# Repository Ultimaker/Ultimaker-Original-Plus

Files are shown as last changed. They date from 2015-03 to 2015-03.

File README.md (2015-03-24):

# Ultimaker-Original-Plus
Bill of Materials and parts for UM-original +

In this repository you will find the documentation and source files for all parts in the Ultimaker-Original+ 3D printer. In the Bill Of Materials (BOM) repository all the parts are numbered and named with the correct amounts. The parts can be found in all the separate directories. 

A lot of parts are lasercut. In the BOM these are marked by the blue colour. The lasercut files can be found separately in the laser file directory. The electronic files can be found in the directory 1091 main board V2.1.1; 1146 ultipanel rev 1.1 and 1155 Print Table Heated Bed.

The manual will explain how to put all files together. 

If you are missing a part or information feel free to file an issue on github.

Harma Woldhuis 
Ultimaker Research and Development

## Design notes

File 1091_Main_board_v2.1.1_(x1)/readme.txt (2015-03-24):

The UltiMainboard 2.x.x electronics are released under GPLv2 license.
And are based on the origonal Ultimaker electronics design by Jan-Jaap Schuurman, Siert Wijnia and ErikDeBruijn at http://reprap.org/wiki/Ultimaker's_v1.5.7_PCB
As well as the ArduinoMega2560 by Arduino: http://arduino.cc/en/Main/arduinoBoardMega2560

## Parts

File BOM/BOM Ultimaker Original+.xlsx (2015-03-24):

 | Ultimaker Original+ |  |  | lasercut parts
 |  |  |  | injection moulded parts
Total quantity parts | 662
Partnummer |  | Naam | Quantity
1002 | A | Front Panel | 1
1003 | A | Back Panel | 1
1004 | A | Left Panel | 1
1005 | A | Right Panel | 1
1006 | A | Top Panel | 1
1007 | A | Bottom Panel | 1
1008 | A | Reel Holder Part A | 1
1009 | A | Reel Holder Mounting Plate | 1
1010 | A | Velcro parts | 4
1011 | A | Y-linear shaft | 2
1012 | A | X-linear shaft | 2
1016 | A | Feeder Quick Fit Coupling | 1
1017 | A | Feeder Motor | 1
1018 | A | Feeder Base Plate Motor Side | 1
1021 | A | Ball Bearing 688-2RS | 10
1023 | A | Limit Switch, Black Long Wire | 1
1025 | A | Limit Switch, Blue Wire | 1
1026 | A | Limit Switch, Red Wire | 1
1028 | A | Z-linear Shaft | 2
1029 | A | Bearing Cap Outside | 8
1031 | A | Feeder Bolt Clip | 1
1032 | A | Feeder Clamp A | 1
1033 | A | Feeder Clamp C | 1
1034 | A | Feeder Clamp B | 1
1035 | A | Feeder Lever | 1
1036 | A | Feeder Wheel | 1
1037 | A | Print Head Coupling Plate | 1
1039 | A | Feeder U bar | 1
1041 | A | Feeder Small Gear | 1
1044 | A | Z-shaft Cap Top | 2
1045 | A | Bearing Cap Inside | 6
1046 | A | Print Head Shaft X,Y | 2
1048 | A | Print Head Hot End Holder | 1
1049 | A | Aluminum Heater Block | 1
1053 | A | Hot End Isolator Tube | 1
1054 | A | Nozzle 0.4mm | 1
1055 | B | Hot End Isolator Coupler | 1
1056 | B | Sintered Bushing | 4
1057 | B | Z-shaft Cap Bottom | 2
1058 | B | Print Head Back | 1
1059 | B | Print Head Top Cap | 1
1061 | B | Print Head Bottom Cap | 1
1062 | B | Print Head Left | 1
1063 | B | Print Head Front | 1
1064 | B | Print Head Right | 1
1065 | A | Linear Bearing LM6LUU | 2
1067 | A | PEEK Isolator | 1
1069 | A | Tube Coupling Collet | 1
1071 | A | Clamp Clip | 2
1082 | A | X,Y-Motor | 2
1084 | A | Timing Pulley 5mm Shaft | 2
1085 | A | Timing Belt B100 MXL | 2
1086 | A | Timing Belt B300 MXL | 4
1088 | A | Timing Pulley 8mm Shaft | 10
1089 | A | Right Side Controller | 1
1091 | B | Main Board V2.1.1 | 1
1092 | A | Left Side Controller | 1
1093 | A | Bottom Cover Controller | 1
1095 | A | Top Cover Controller | 1
1097 | A | Spiral Sleeve | 1
1116 | A | Reel Holder Part B | 4
1117 | A | Sliding Block Part A | 8
1118 | A | Sliding Block Part B | 1
1119 | A | Sliding Block Part C | 2
1121 | A | Sliding Block Part D | 4
1122 | A | Sliding Block Part E | 1
1126 | A | Feeder Middle Plate | 1
1128 | A | Feeder Big Gear | 1
1129 | A | Knob | 1
1131 | A | Cable Duct Front | 2
1132 | A | Cable Duct Back | 2
1133 | A | Feeder Knurled Bolt | 1
1134 | A | Capnut M8 | 1
1136 | A | Washer M8 | 2
1137 | A | Nut M8 | 1
1139 | A | Spacer, White, 3.2x5x16 | 4
1142 | A | Ball Bearing 693ZZ | 1
1143 | A | Feeder Spring D2110 | 1
1144 | A | USB Cable | 1
1146 | A | Ultipanel Rev 1.1 | 1
1152 | A | Table Spring D2150 | 3
1154 | A | Print Table Glass | 1
1155 | A | Print Table Heated Bed | 1
1159 | A | Z-Motor with Trapezoidal Lead Screw | 1
1170 | A | Square Flanged Linear Bearing LMK12LUU | 2
1171 | A | Double flat Cable 10 Wire | 1
1183 | B | Heated Bed Cable | 1
1185 | A | PT100 B sensor | 1
1187 | A | Trapezoidal Lead Nut | 1
1201 | B | Washer Large M3 | 14
1202 | B | ISO 7380 M3x10 | 23
1203 | B | ISO 7380 M3x12 | 11
1204 | B | ISO 7380 M3x16 | 75
1205 | B | ISO 7380 M3x14 | 7
1206 | B | ISO 7380 M3x20 | 12
1207 | B | ISO 7380 M3x25 | 12
1208 | B | ISO 7380 M3x30 | 16
1209 | B | Nut M3 | 110
1211 | A | Set Screw M4x4 | 12
1214 | A | ISO 7040 Nut M3 Prev. torque A2 | 25
1217 | A | ISO 7380 M4x10 A2 | 8
1225 | A | tape | 1
1226 | A | grease | 1
1227 | A | Hex Key Screwdriver 2 | 1
1228 | A | pritt | 1
1238 | A | Power Adapter 24v-220W | 1
1241 | A | Motor Spacer | 2
1243 | A | Heated Bed Cable Clip | 1
1250 | A | SD card 4G | 1
1256 | A | Build Platform Glass Retainer Back | 4
1257 | A | Knurled Nut Platform | 3
1266 | C | Bowden tube | 1
1288 | A | Washer M6 | 3
1315 | A | Jumper | 2
1326 | A | Warning sticker | 1
1348 | A | Bolt M3x4 | 2
1362 | A | Tap Fix 2.5x14 mm staal verzinkt bolkop porzidrive | 2
1355 | B | Heated Bed Bolt 8 mm
1356 | B | Heated Bed Bolt 20 mm
1402 | A | Hex Key Wrench 2.5 | 1
1501 | D | Print Head Fancap Metal | 1
1502 | A | Spacer 3.2x6x8 | 8
1503 | A | Sliding Block Part F | 8
1504 | A | Sliding Block Part G | 4
1505 | A | print table cap | 1
1506 | A | print table cap side A | 1
1507 | A | print table cap side B | 1
1508 | A | print table cap middle | 2
1509 | A | Feeder cap | 1
1510 | A | Feeder wheelcap | 1
1511 | A | Short reel holder part A | 2
1512 | A | Print Head Fan 24VDC | 1
1513 | A | Heater Cartridge 24V 40W | 1
1514 | A | Metal Cable Clamp | 1
1522 | A | ulticontroller window | 1
1524 | B | copper grease | 1
1528 | A | Feeder Plate Non Motor Side | 1
1529 | A | Electronics Cover Plate | 1
1530 | A | X-Y calibration sticks | 2
1540 | A | Nylon M3 nut | 10
1541 | A | Nylon M3x 12 Panhead | 6
1542 | A | Nylon M3x 25 Panhead | 4
1545 | A | Spacer 3.2x6x3 | 2
1680 | A | Print Head Thumb screw 62mm | 4
1681 | A | Timingbelt spring | 4
1805 | 01 | Power Cable EU Type C13 CE
1806 | 01 | Power Cable UK Type C13 CE
1807 | 01 | Power Cable AU Type C13 CE
1808 | 01 | Power Cable US Type C13 CE
1818 | B | Print Table Base Plate | 1
Reserve onderdelen
1201 | B | Washer Large M3 | 5
1202 | B | ISO 7380 M3x10 | 5
1203 | B | ISO 7380 M3x12 | 5
1204 | B | ISO 7380 M3x16 | 5
1205 | B | ISO 7380 M3x14 | 5
1206 | B | ISO 7380 M3x20 | 5
1207 | B | ISO 7380 M3x25 | 5
1208 | B | ISO 7380 M3x30 | 5
1209 | B | Nut M3 | 10
1211 | A | Set Screw M4x4 | 5
1214 | A | ISO 7040 Nut M3 Prev. torque A2 | 10
1215 | A | ISO 10642 M3x8 A2 | 2
1216 | A | ISO 10642 M3x20 A2 | 2
1217 | A | ISO 7380 M4x10 A2 | 2
1540 | A | Nylon M3 nut | 2
1541 | A | Nylon M3x 12 Panhead | 2
1542 | A | Nylon M3x 25 Panhead | 2

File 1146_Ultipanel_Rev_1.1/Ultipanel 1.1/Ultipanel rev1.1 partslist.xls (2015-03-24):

Part | RS partno | Manufacturer partno | Value | Device | Package | Remarks
724-3175 | 724-3175 | RS 724-3175 |  |  |  | buzzer
DS1 | 532-6818 | Displaytech 204A-CC-BC-3LP |  |  |  | lcd screen Blue/White, soldered with header 2.54 mm
EC11E15244B2 | 729-5609 | ALPS EC11E15244B2 |  |  |  | 20mm Vertical encoder 15 Pulses 30 DET
EXP1 | 473-8349 | TE connectivity 1-1634689-0 |  |  |  | right angle!
EXP2 | 473-8349 | TE connectivity 1-1634689-0 |  |  |  | right angle!
HRS163_REVERSE | 685-0788 | Hirose DM1B-DSF-PEJ(82)
R3 | 731-2883 | Panasonic EVM3YSX50B14 | 10K
RBEEP | 708-6014 |  | 440R |  | 0805
RLED | 721-9725 |  | 68R |  | 1206
SHIFT | 483-6544P | NXP 74HC4050D | 4050D |  |  | levelshifter
T4 | 294-312 | Magnatec 2N3904 | 2N3904
JP1 | not used

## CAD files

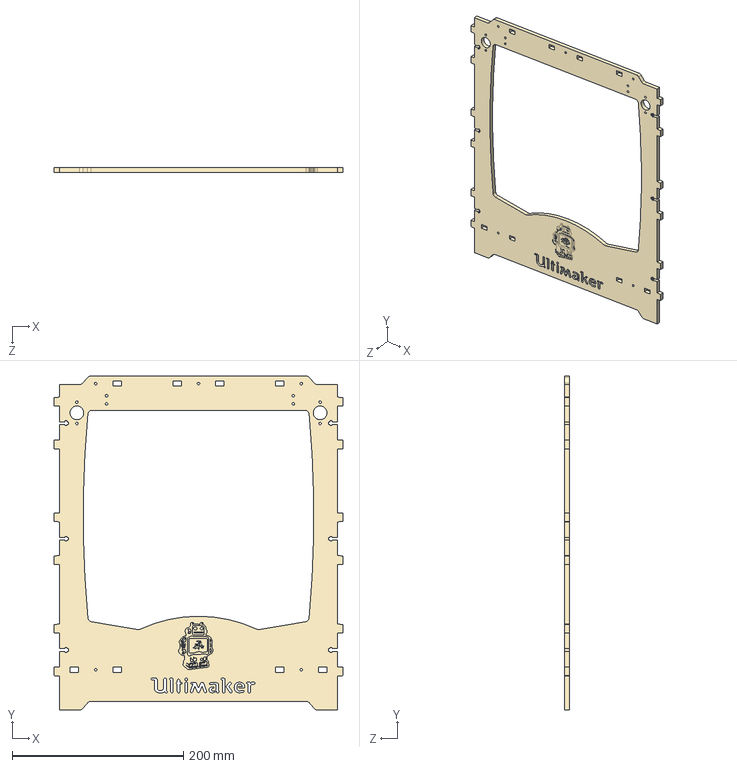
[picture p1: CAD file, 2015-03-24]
1002_Front_Panel/1002-A2P-A.STEP
337.2 x 390.0 x 6.00 mm

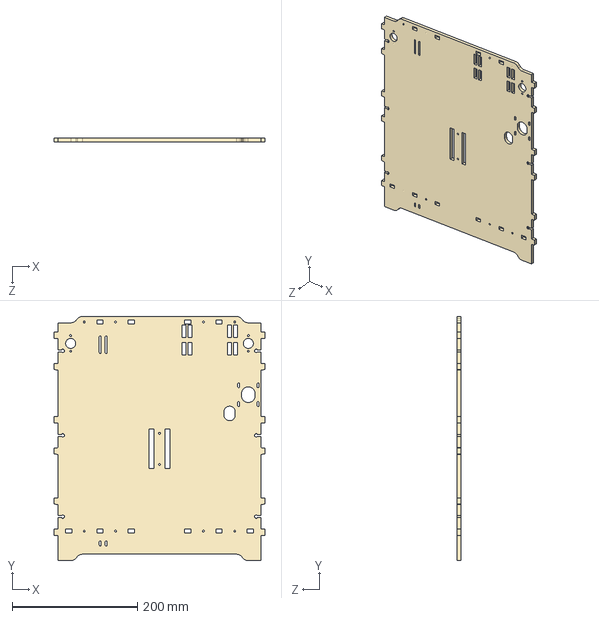
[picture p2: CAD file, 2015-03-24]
1003_Back_Panel/1003-A2P-A.STEP
337.2 x 390.0 x 6.00 mm

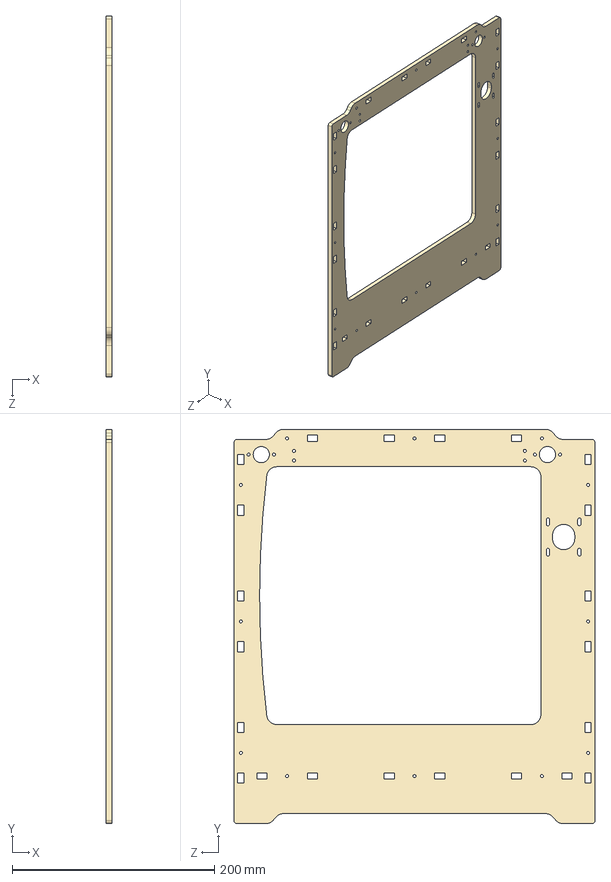
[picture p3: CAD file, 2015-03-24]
1004_Left_Panel/1004-A2P-A.STEP
6.00 x 390.0 x 357.0 mm

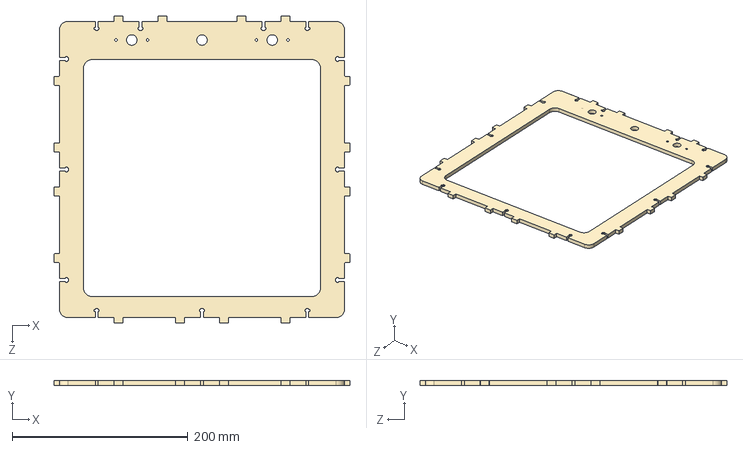
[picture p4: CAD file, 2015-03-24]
1006_Top_Panel/1006-A2P-A.STEP
337.2 x 6.00 x 349.7 mm

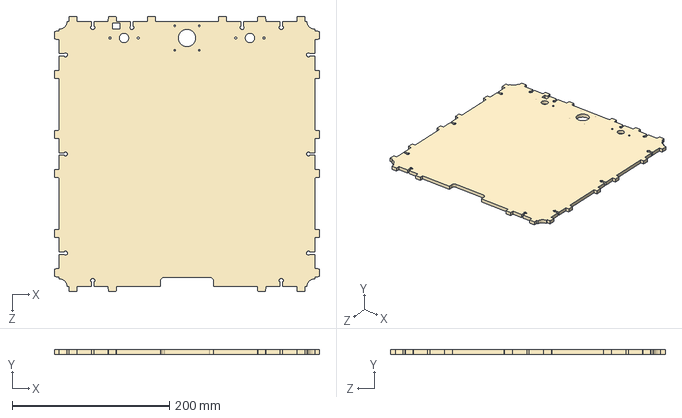
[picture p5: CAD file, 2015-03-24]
1007_Bottom_Panel/1007-A2P-A.STEP
337.2 x 6.00 x 349.7 mm

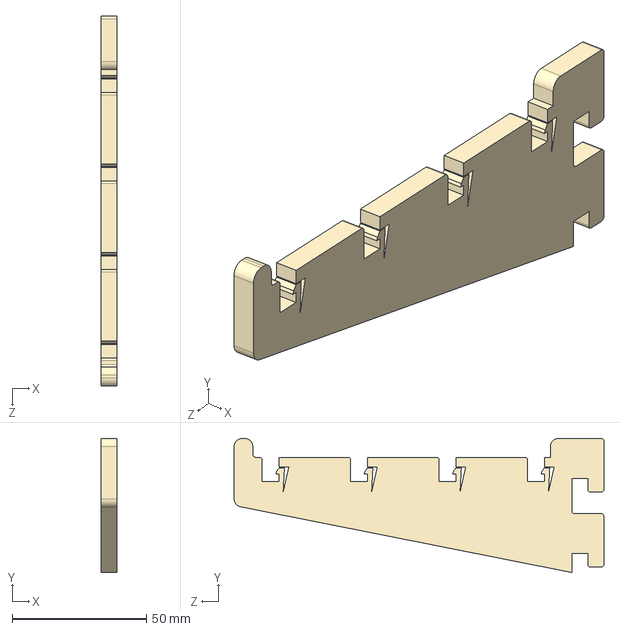
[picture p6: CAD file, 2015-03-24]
1008_Reel_Holder_Part_A/1008-A2P-A.STEP
6.00 x 50.0 x 138.0 mm

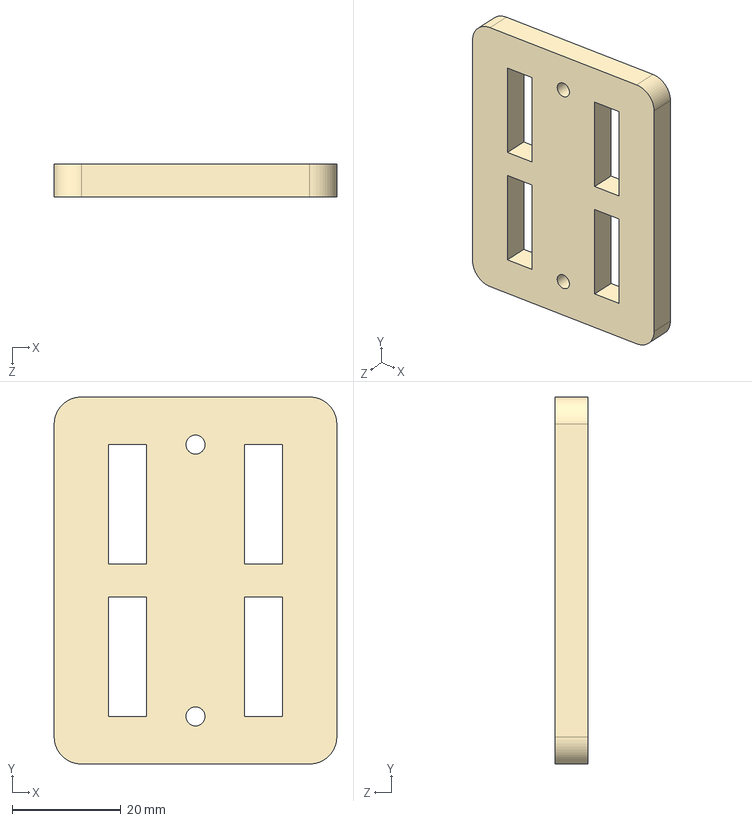
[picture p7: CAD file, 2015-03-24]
1009_Reel_Holder_Mounting_Plate/1009-A2P-A.STEP
52.0 x 67.5 x 6.00 mm

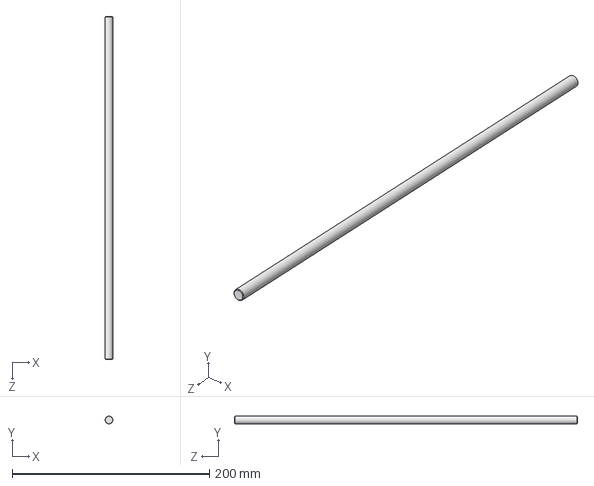
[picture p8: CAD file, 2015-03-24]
1011_Y-linear_shaft/1011-A2P-A.STEP
7.99 x 8.00 x 348.0 mm

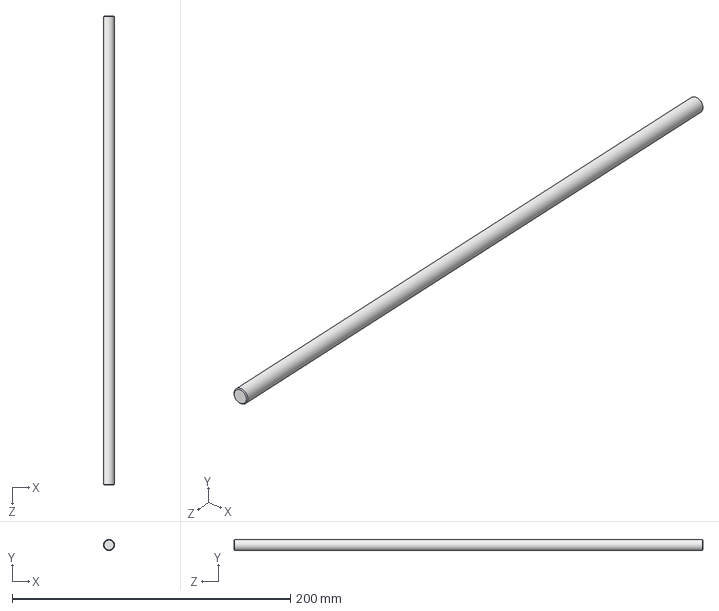
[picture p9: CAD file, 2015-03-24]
1012_X-linear_shaft/1012-A2P-A.STEP
7.99 x 8.00 x 337.0 mm

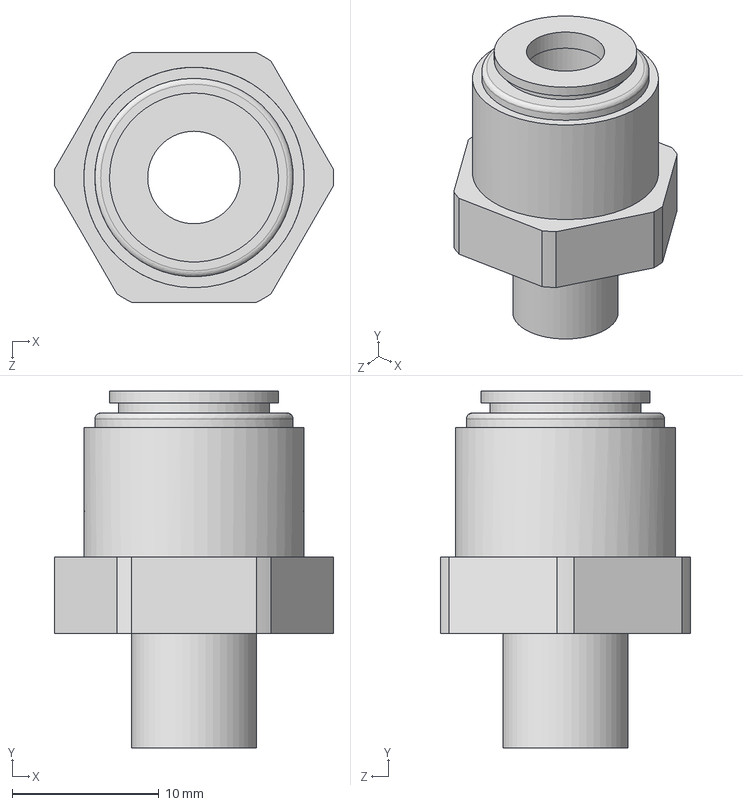
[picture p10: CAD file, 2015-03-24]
1016_Feeder_Quick_Fit_Coupling/1016-Z1P-A.STEP
19.0 x 24.3 x 17.0 mm

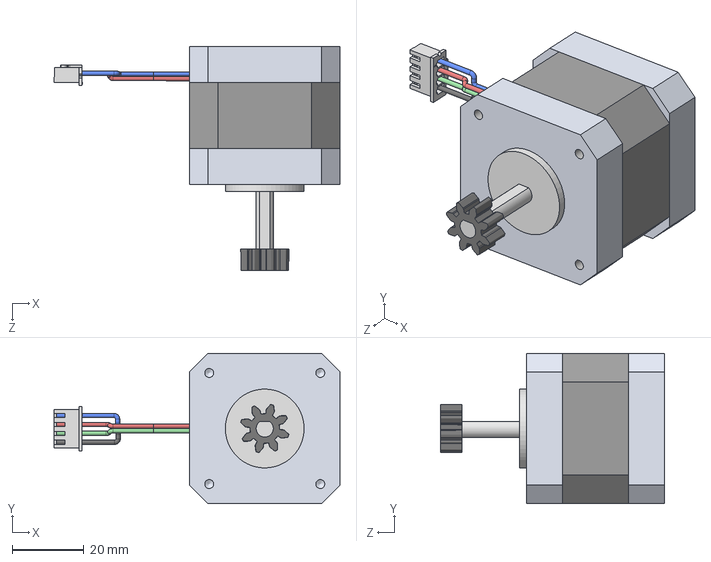
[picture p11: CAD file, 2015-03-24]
1017_Feeder_Motor/1017-Z1P-A.STEP
79.8 x 42.0 x 62.5 mm

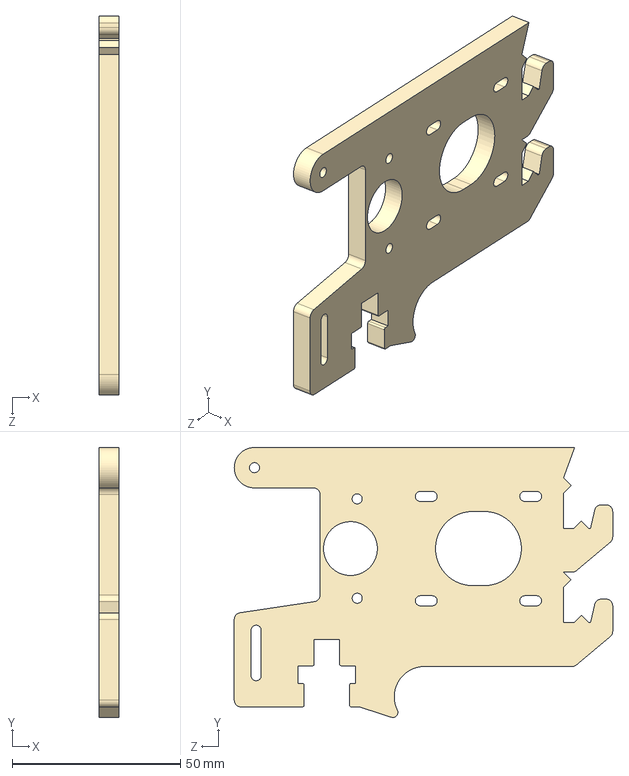
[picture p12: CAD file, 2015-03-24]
1018_Feeder_Base_Plate_Motor_Side/1018-A2P-A.STEP
6.00 x 80.1 x 112.4 mm

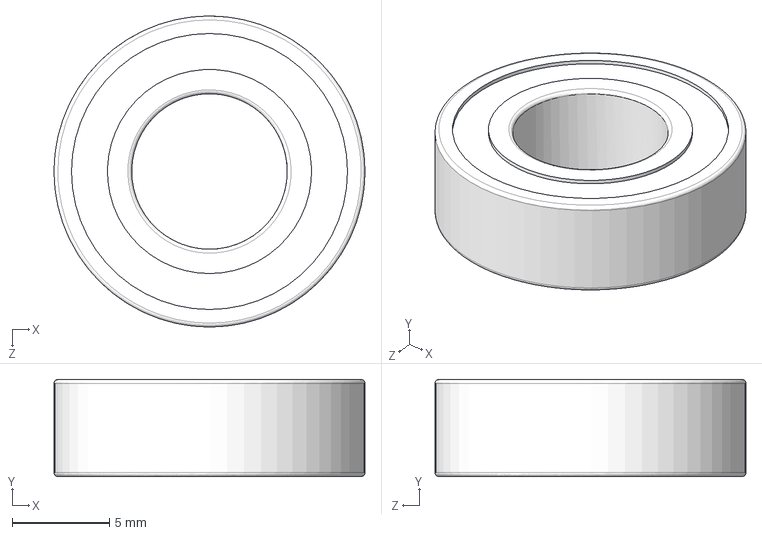
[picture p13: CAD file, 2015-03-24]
1021_Ball_Bearing_688-2RS/1021-Z1P-A.STEP
16.0 x 5.00 x 16.0 mm

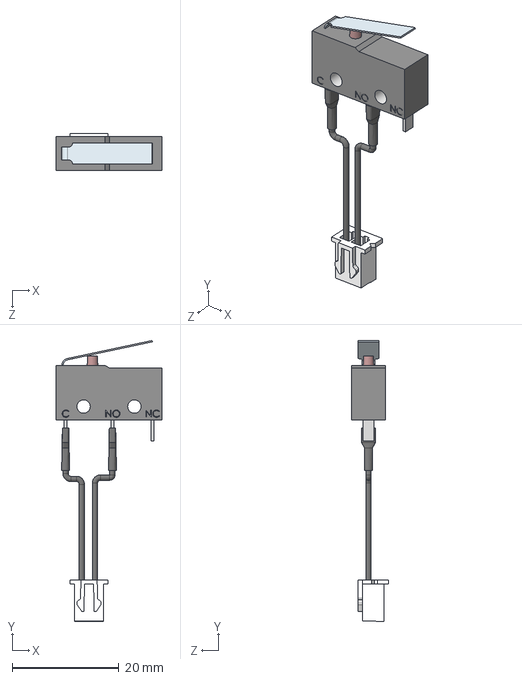
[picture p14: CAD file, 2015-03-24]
1023_Limit_Switch,_Black_Long_Wire/1023-Z1P-A.STEP
19.8 x 52.7 x 6.90 mm

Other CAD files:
1005_Right_Panel/1005-A2P-A.STEP
1025_Limit_Switch,_Blue_Wire/1025-Z1P-A.STEP
1026_Limit_Switch,_Red_Wire/1026-Z1P-A.STEP
1028_Z-linear_Shaft/1028-A2P-A.STEP
1029_Bearing_Cap_Outside/1029-A2P-A.STEP
1031_Feeder_Bolt_Clip/1031-A2P-A.STEP
1032_Feeder_Clamp_A/1032-A2P-A.STEP
1033_Feeder_Clamp_C/1033-A2P-A.STEP
1034_Feeder_Clamp_B/1034-A2P-A.STEP
1035_Feeder_Lever/1035-A2P-A.STEP
1036_Feeder_Wheel/1036-A2P-A.STEP
1037_Print_Head_Coupling_Plate/1037-A2P-A.STEP
1039_Feeder_U_bar/1039-A2P-A.STEP
1041_Feeder_Small_Gear/1041-A2P-A.STEP
1044_Z-shaft_Cap_Top/1044-A2P-A.STEP
1045_Bearing_Cap_Inside/1045-A2P-A.STEP
1046_Print_Head_Shaft_X,Y/1046-A2P-A.STEP
1048_Print_Head_Hot_End_Holder/1048-A2P-A.STEP
1049_Aluminum_Heater_Block/1049-A2P-A.STEP
1053_Hot_End_Isolator_Tube/1053-A2P-A.STEP
1054_Nozzle_0.4mm/1054-A2P-A.STEP
1055_Hot_End_Isolator_Coupler/1055-A2P-B.STEP
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

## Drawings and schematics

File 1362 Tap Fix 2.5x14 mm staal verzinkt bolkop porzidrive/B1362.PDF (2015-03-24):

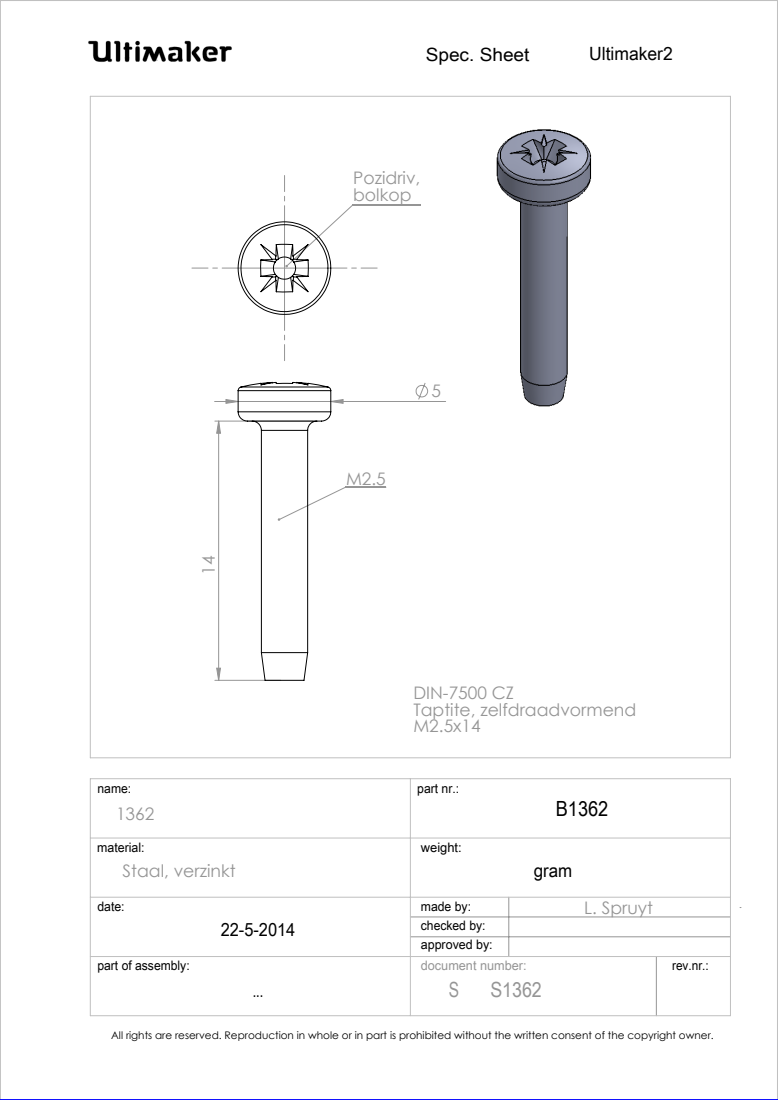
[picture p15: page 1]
part of assembly:; rev.nr.:; part nr.:; made by:; Spec. Sheet; approved by:; checked by:; L. Spruyt; document number: S S1362; Staal, verzinkt; DIN-7500 CZ Taptite, zelfdraadvormend

All rights are reserved. Reproduction in whole or in part is prohibited without the written consent of the copyright owner.

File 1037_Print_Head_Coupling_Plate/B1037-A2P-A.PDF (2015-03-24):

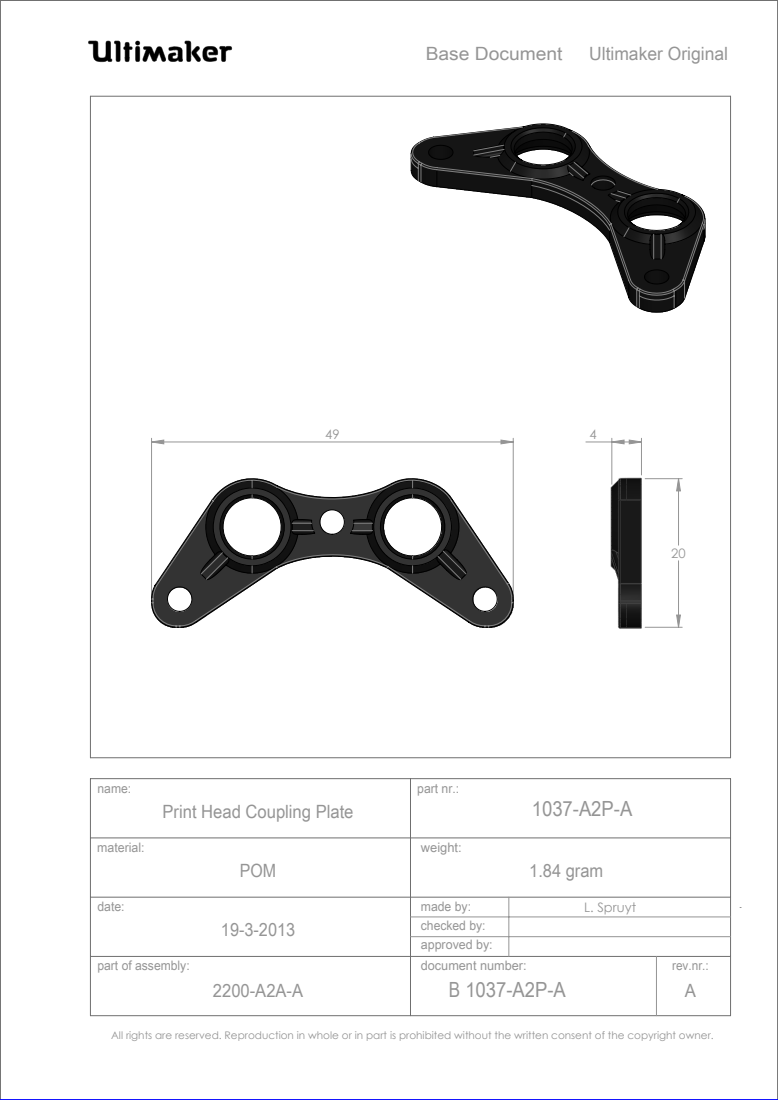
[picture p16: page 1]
POM; 1.84 gram; Ultimaker Original; part of assembly:; rev.nr.:; part nr.:; made by:; Base Document; approved by:; checked by:; L. Spruyt; document number: B 1037-A2P-A

name:
Print Head Coupling Plate

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

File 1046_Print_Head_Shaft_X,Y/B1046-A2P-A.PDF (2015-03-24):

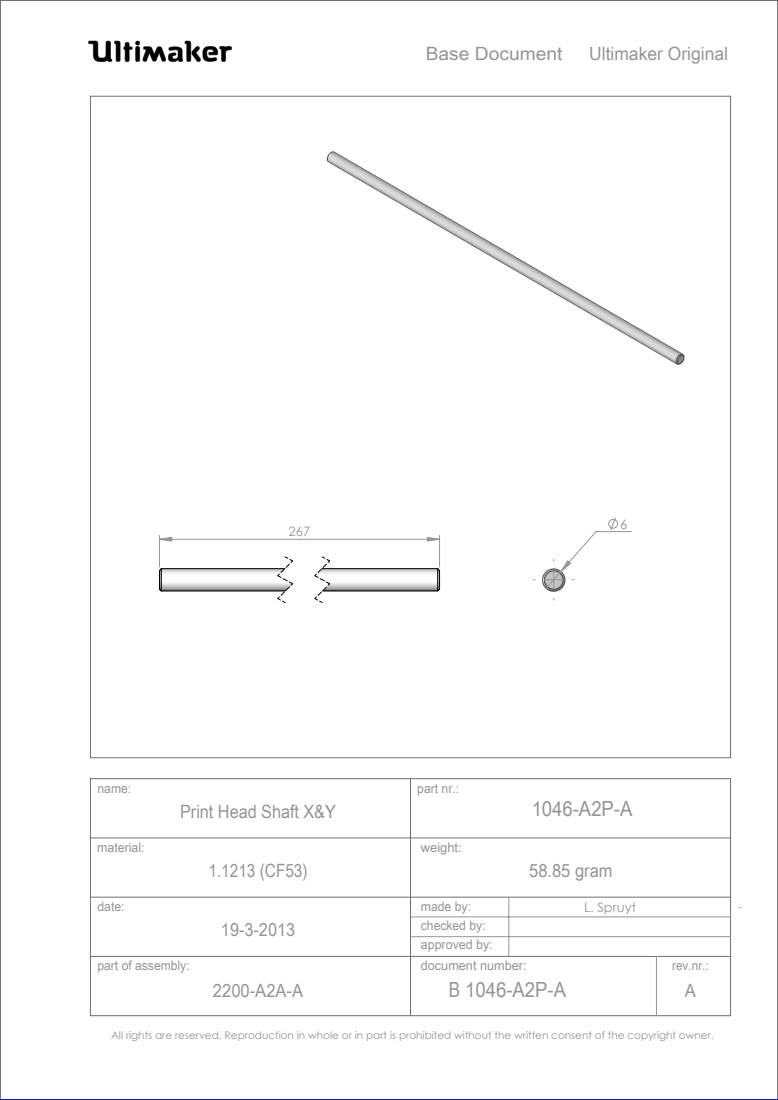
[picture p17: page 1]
58.85 gram; Ultimaker Original; part of assembly:; rev.nr.:; part nr.:; made by:; Base Document; approved by:; checked by:; L. Spruyt; document number: B 1046-A2P-A

Print Head Shaft X&Y

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

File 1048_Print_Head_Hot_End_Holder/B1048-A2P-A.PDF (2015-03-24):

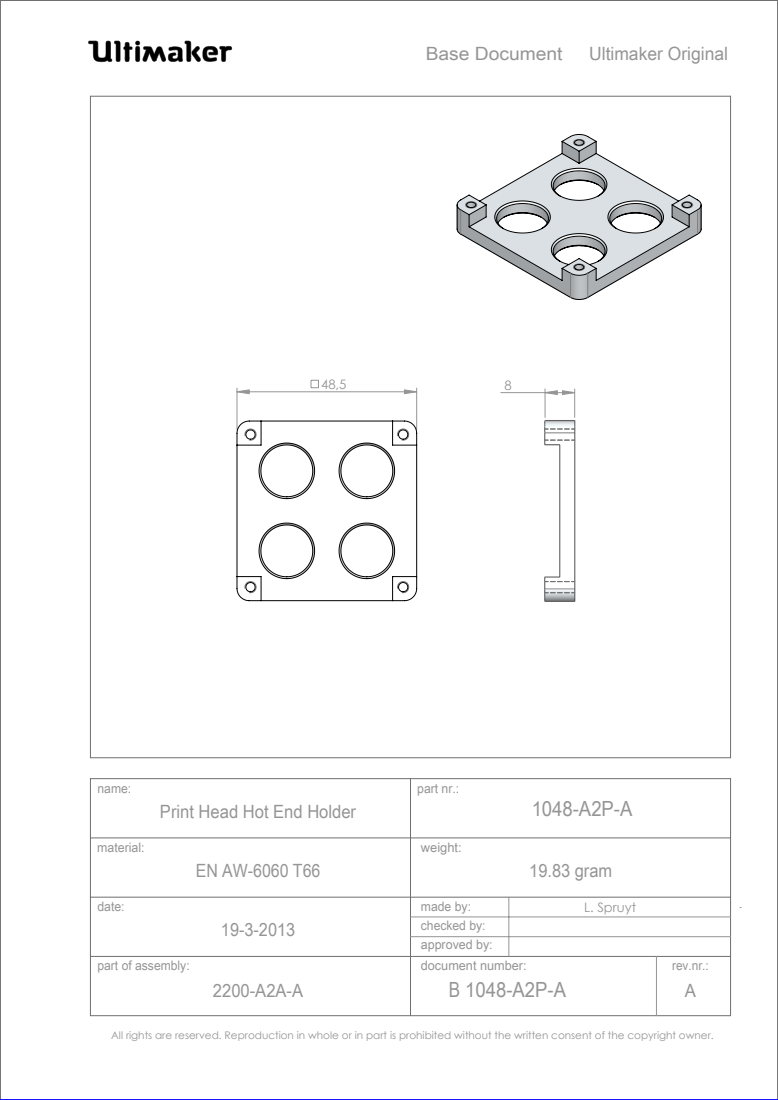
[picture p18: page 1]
19.83 gram; Ultimaker Original; part of assembly:; rev.nr.:; part nr.:; made by:; Base Document; approved by:; checked by:; L. Spruyt; document number: B 1048-A2P-A

name:
Print Head Hot End Holder

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

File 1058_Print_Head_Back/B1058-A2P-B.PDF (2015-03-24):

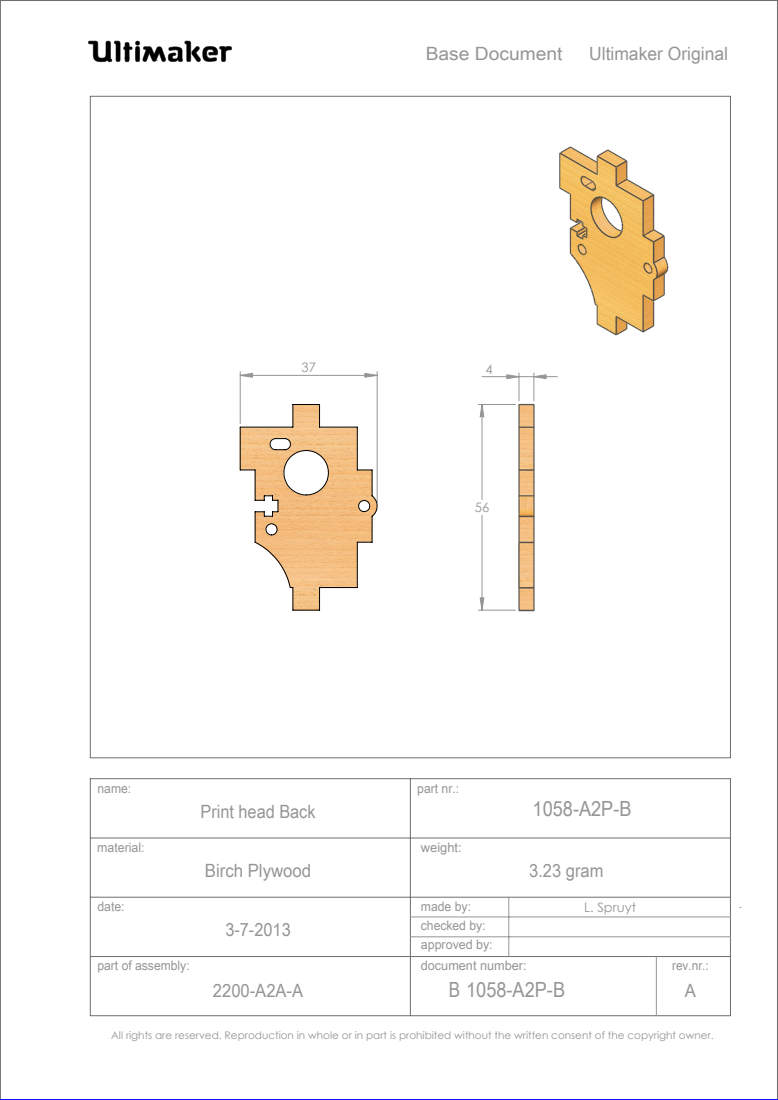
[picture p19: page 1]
Birch Plywood; 3.23 gram; Ultimaker Original; part of assembly:; rev.nr.:; part nr.:; made by:; Base Document; approved by:; checked by:; L. Spruyt; document number: B 1058-A2P-B

Print head Back

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

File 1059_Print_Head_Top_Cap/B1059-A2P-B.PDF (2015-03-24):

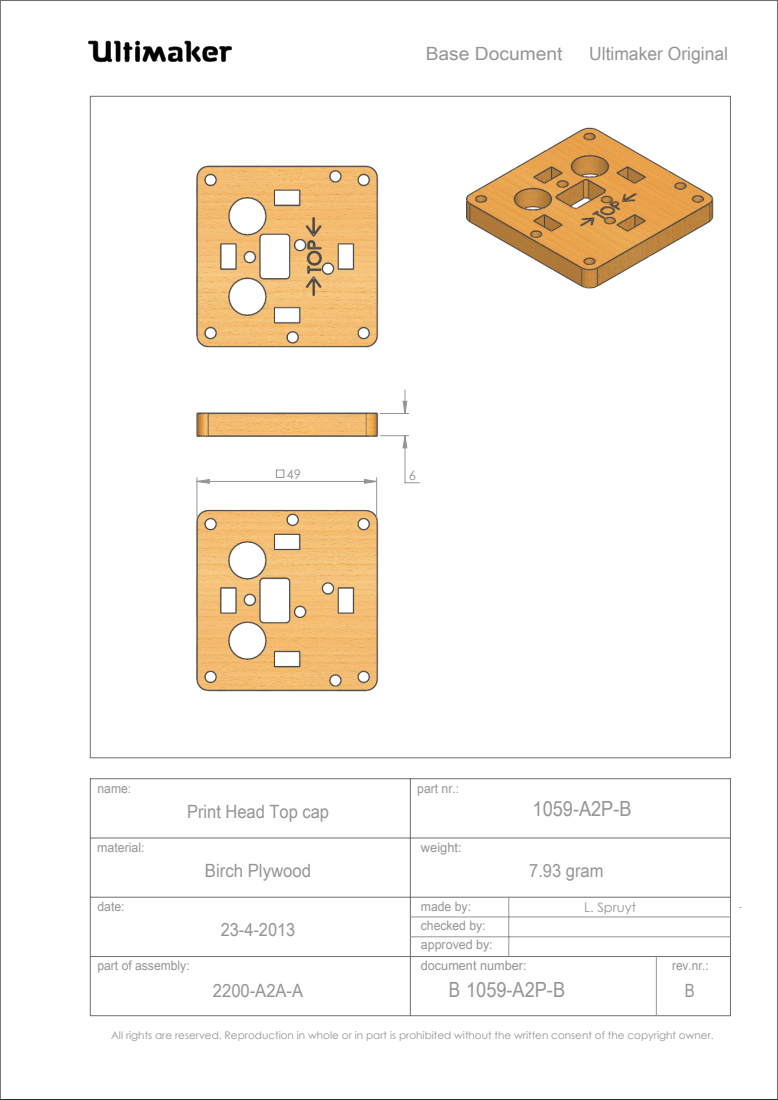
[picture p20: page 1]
Birch Plywood; 7.93 gram; Ultimaker Original; part of assembly:; rev.nr.:; part nr.:; made by:; Base Document; approved by:; checked by:; L. Spruyt; document number: B 1059-A2P-B

Print Head Top cap

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

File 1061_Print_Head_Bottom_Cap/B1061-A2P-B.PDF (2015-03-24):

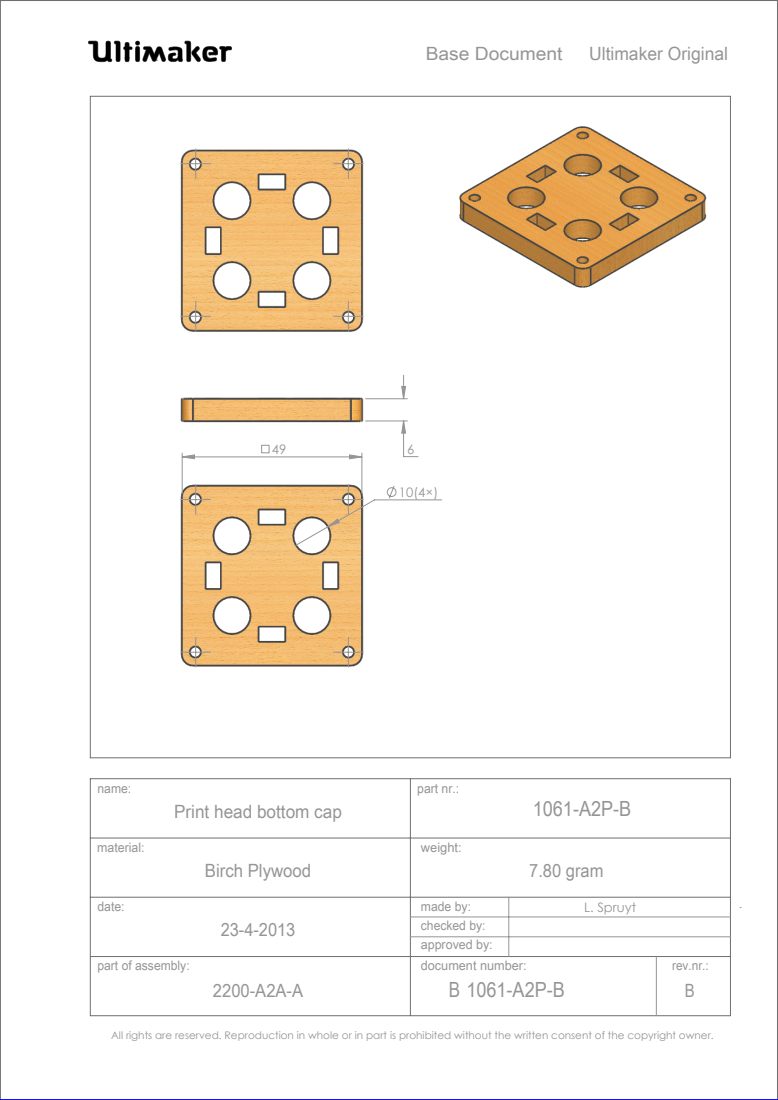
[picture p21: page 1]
Birch Plywood; 7.80 gram; Ultimaker Original; part of assembly:; rev.nr.:; part nr.:; made by:; Base Document; approved by:; checked by:; L. Spruyt; document number: B 1061-A2P-B

Print head bottom cap

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

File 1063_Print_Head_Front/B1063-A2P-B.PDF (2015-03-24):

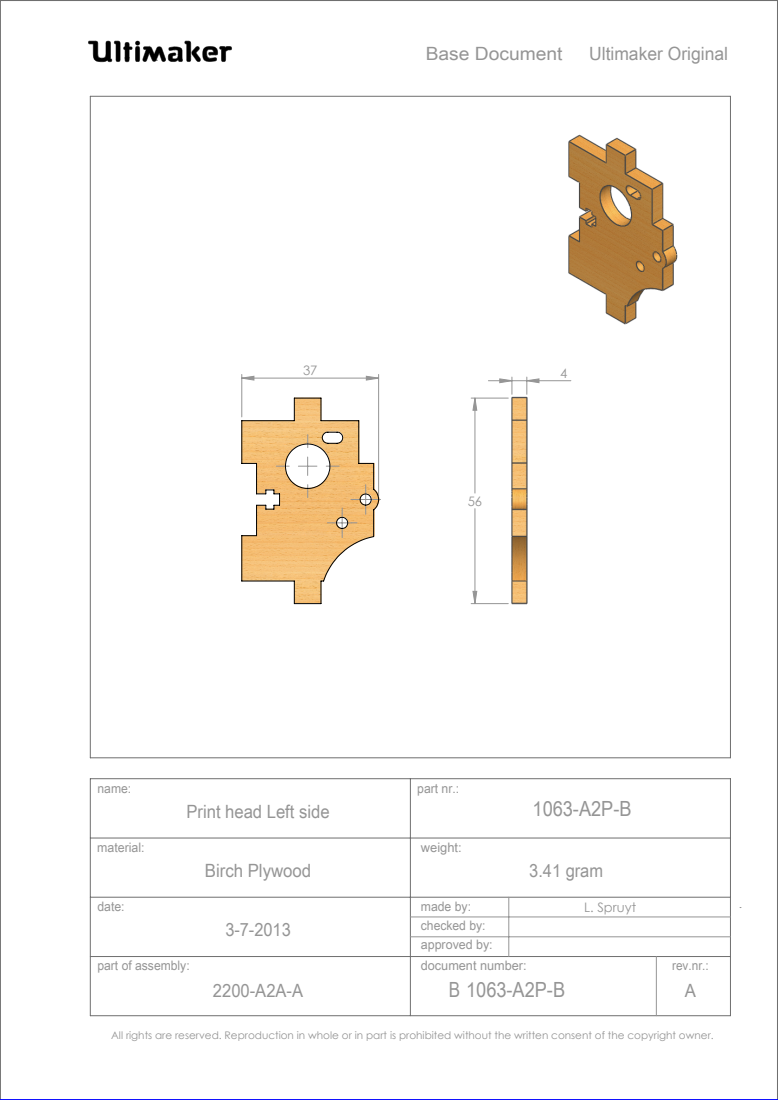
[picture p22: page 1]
Birch Plywood; 3.41 gram; Ultimaker Original; part of assembly:; rev.nr.:; part nr.:; made by:; Base Document; approved by:; checked by:; L. Spruyt; document number: B 1063-A2P-B

Print head Left side

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

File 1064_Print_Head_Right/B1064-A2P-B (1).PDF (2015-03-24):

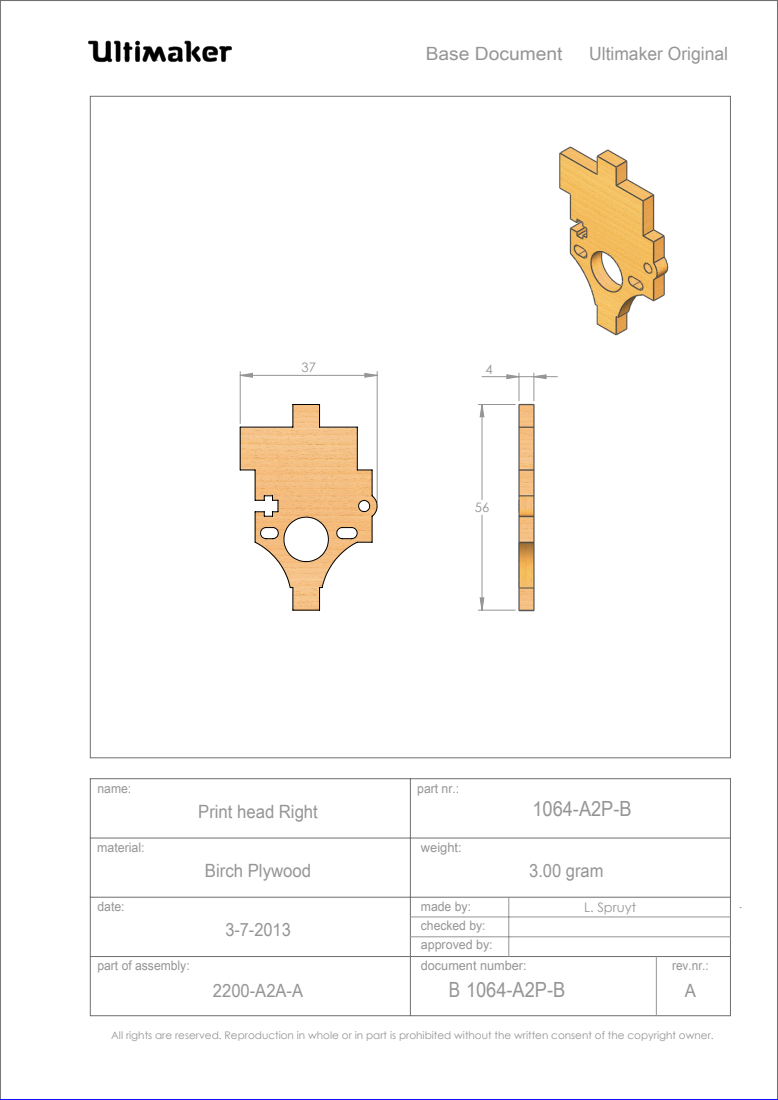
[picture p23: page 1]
Birch Plywood; 3.00 gram; Ultimaker Original; part of assembly:; rev.nr.:; part nr.:; made by:; Base Document; approved by:; checked by:; L. Spruyt; document number: B 1064-A2P-B

Print head Right

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

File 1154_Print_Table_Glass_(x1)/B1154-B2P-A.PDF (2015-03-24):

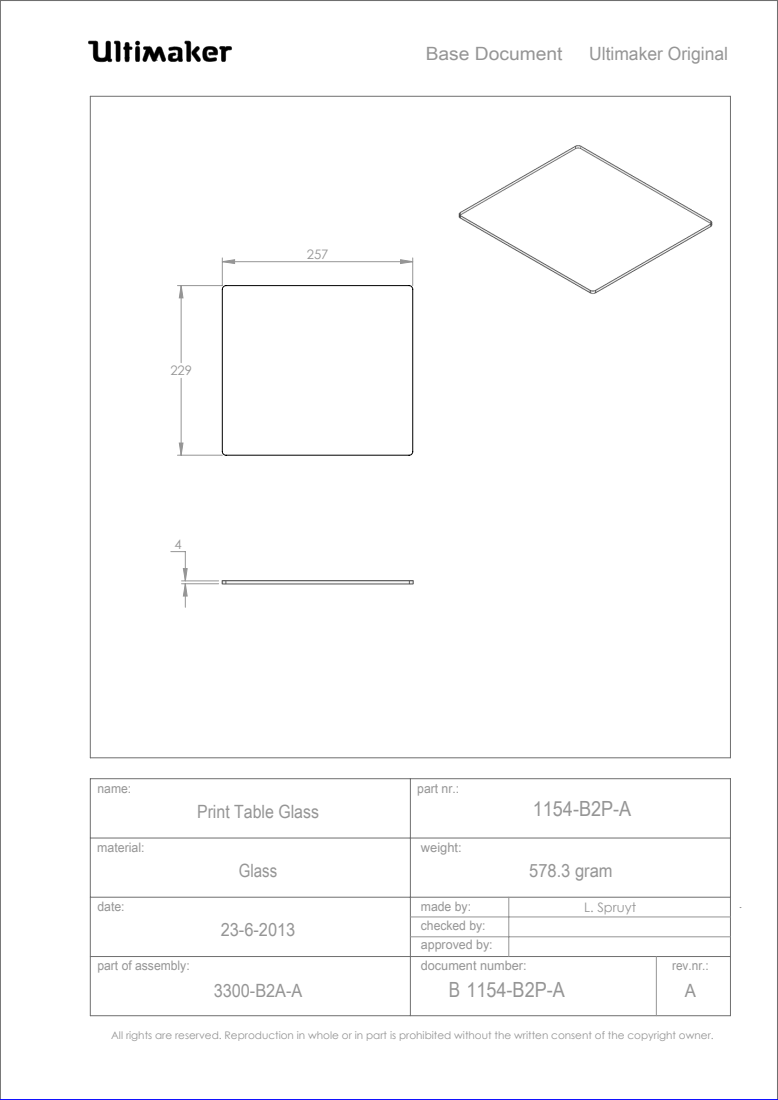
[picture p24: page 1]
Glass; 578.3 gram; Ultimaker Original; part of assembly:; rev.nr.:; part nr.:; made by:; Base Document; approved by:; checked by:; L. Spruyt; document number: B 1154-B2P-A

Print Table Glass

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

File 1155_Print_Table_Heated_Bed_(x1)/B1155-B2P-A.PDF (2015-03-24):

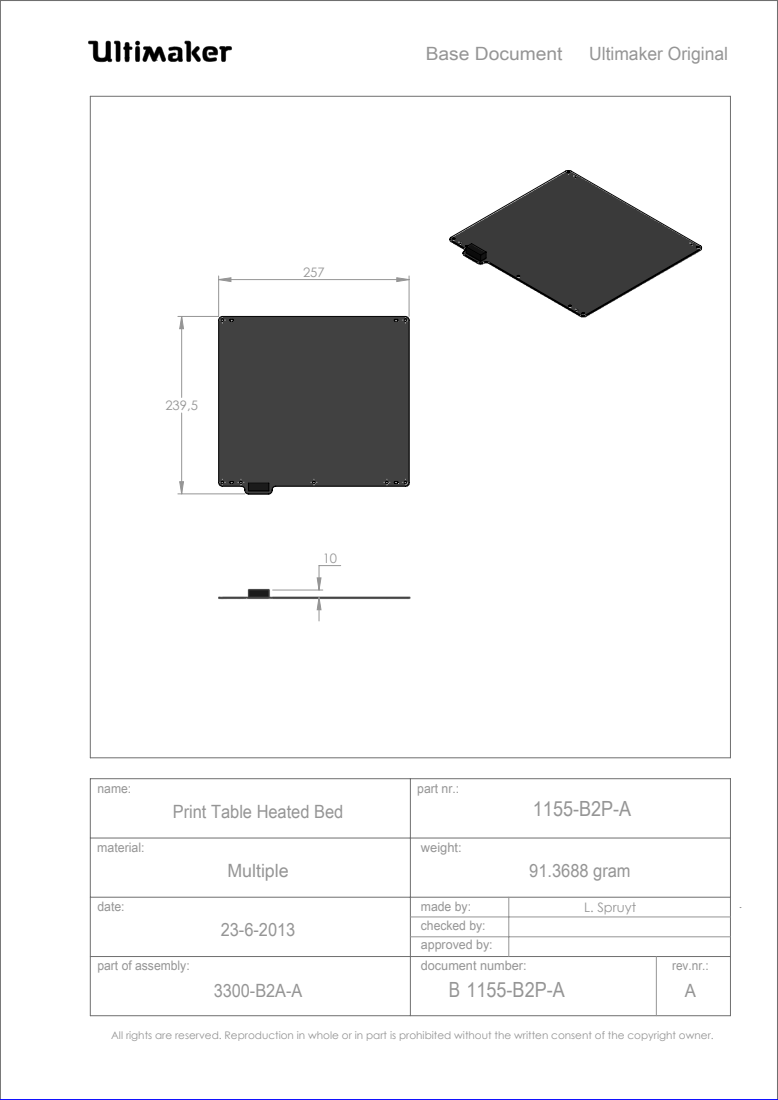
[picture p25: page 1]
Multiple; 91.3688 gram; Ultimaker Original; part of assembly:; rev.nr.:; part nr.:; made by:; Base Document; approved by:; checked by:; L. Spruyt; document number: B 1155-B2P-A

name:
Print Table Heated Bed

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

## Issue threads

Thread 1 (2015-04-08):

Missing heated bed designing file

kqkq, 2015-04-08:
The part `1155 Print Table Heated Bed` is an electronic part. But there's only a 3D model available. How can I get an EDA file (e.g. Eagle or Altium PCB file) ?

daid, 2015-04-08:
The part is the same as in the Ultimaker2, so the files should be there as well.

kqkq, 2015-04-09:
@daid

No, the EDA file is not there either. I open an issue (https://github.com/Ultimaker/Ultimaker2/issues/10) EIGHT month ago and no one reply.

harmawoldhuis, 2015-05-05:
I'm sorry it took so long. I uploaded the correct files a few weeks ago.

2015-04-09 12:36 GMT+02:00 KUANG Qi <notifications@github.com>:

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

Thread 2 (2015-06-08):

Countersunk Bolts M3x20 (1216)

BlietZ, 2015-06-08:
item is used on page 63 of assembly guide. Chapter: 6.4.3. Step 3: Connecting the PCB to the Baseplate

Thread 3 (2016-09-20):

Missing Assembly

imaluschi, 2016-09-20:
Hi, there is an assembly of other Ultimaker Printers, but from Original-Plus are only the parts available.

Because i need the Assembly of the Extrusion head i assembled ist, you find it below. Maybe other assemblies will follow.

[6.2_Extrusion Head.zip](https://github.com/Ultimaker/Ultimaker-Original-Plus/files/482874/6.2_Extrusion.Head.zip)

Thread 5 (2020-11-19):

1046_Print_Head_Shaft_X,Y

kesjeff, 2020-11-19:
I don't think the lengths of the print head shafts are correct.  Ultimaker 2 and I remember the older files for the Ultimaker original had two different shaft lengths. But it doesn't seem to be that way now so I thought I would see if this is incorrect and needs to be more like the UM2 printer.
